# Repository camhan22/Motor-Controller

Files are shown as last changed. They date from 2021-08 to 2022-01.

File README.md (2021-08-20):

# Motor-Controller

12-48VDC 65A continuous (150A Peak) 0-100% duty cycle brushed DC motor driver 

Communicates to a master controller through I2C with commands that look like the following:

DSSSSSSS

Where D is the direction (0 or 1) (1 will apply +VDC to Motor+ Terminal) (0 Will apply +VDC to the Motor- Terminal)
S is the duty cycle from 0-100% (This is checked by the software to ensure it is within bounds) (Anything out of bounds is clamped to 100%)

I2C address can be changed with the dip switches on the board and allows up to 8 motor drivers to run at the same time.

Returns a status byte to describe what the controller is doing. If faults are present, there are seperate status codes for each failure and can be found within the code folder in the controller status codes excel sheet.

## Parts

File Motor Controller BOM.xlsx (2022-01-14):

Schematic Annotation | Part Number | Description | Qty | Price | Supplier | Total Cost | Link
C7,C10,C11,C12 | 399-17501-1-ND | ±5% 50V Ceramic Capacitor X7R 1812 (4532 Metric) 0.1uF | 4 | $1.09 | Digikey | $4.36 | https://www.digikey.com/en/products/detail/kemet/C1812C104J5RAC7800/2235598
C8 | 445-173162-1-ND | 1 µF ±10% 100V Ceramic Capacitor X7R Radial | 1 | $0.73 | Digikey | $0.73 | https://www.digikey.com/en/products/detail/tdk-corporation/FG16X7R2A105KNT06/5811767
C3,C4 | 1189-4388-ND | 2200 µF 50 V Aluminum Electrolytic Capacitors Radial, Can - 10000 Hrs @ 105°C | 2 | $2.84 | Digikey | $5.68 | https://www.digikey.com/en/products/detail/rubycon/50ZLJ2200M18X25/10437363
C9 | 478-10901-1-ND | CAP CER 620PF 100V NP0 1210 | 1 | $0.49 | Digikey | $0.49 | https://www.digikey.com/en/products/detail/avx-corporation/12101A621JAT2A/1605218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
R3,R4,R9,R10 | 541-15.0KACCT-ND | 15 kOhms ±1% 0.75W, 3/4W Chip Resistor 2010 (5025 Metric) Automotive AEC-Q200 Thick Film | 4 | $0.30 | Digikey | $1.20 | https://www.digikey.com/en/products/detail/vishay-dale/CRCW201015K0FKEF/1198590
D1 | 1080-1419-1-ND | Green 570nm LED Indication - Discrete 2.1V 1206 (3216 Metric) | 1 | $0.37 | Digikey | $0.37 | https://www.digikey.com/en/products/detail/QTLP650D4TR/1080-1419-1-ND/2676153?itemSeq=373167869
D2 | 1516-QBLP601-RYCT-ND | Red, Yellow 630nm Red, 591nm Yellow LED Indication - Discrete 2V Red, 2V Yellow 0603 (1608 Metric) | 1 | $0.43 | Digikey | $0.43 | https://www.digikey.com/en/products/detail/qt-brightek-qtb/QBLP601-RY/10322678
R7,R8 | 311-150LJCT-ND | 150 Ohms ±1% 0.25W, 1/4W Chip Resistor 1206 (3216 Metric) Automotive AEC-Q200, Moisture Resistant Thick Film | 2 | $0.10 | Digikey | $0.20 | https://www.digikey.com/en/products/detail/AC1206FR-07150RL/311-150LJCT-ND/2828161?itemSeq=373168587
Q1-Q4 | IRFS3306TRLPBFCT-ND | N-Channel 60 V 120A (Tc) 230W (Tc) Surface Mount D2PAK | 4 | $2.58 | Digikey | $10.32 | https://www.digikey.com/en/products/detail/infineon-technologies/IRFS3306TRLPBF/1925291
U3 | 620-1772-1-ND | Motor Driver NMOS Parallel | 1 | $1.64 | Digikey | $1.64 | https://www.digikey.com/en/products/detail/allegro-microsystems/A4956GESTR-T/5809983
U1 | 175-MAX17640BATA+-ND | Buck Switching Regulator IC Positive Fixed 5V 1 Output 400mA 8-WFDFN | 1 | $1.65 | Digikey | $1.65 | https://www.digikey.com/en/products/detail/maxim-integrated/MAX17640BATA/14287859
L1 | 587-3070-1-ND | 68 µH Unshielded Wirewound Inductor 410 mA 1.3Ohm Max 1210 (3225 Metric) | 1 | $0.30 | Digikey | $0.30 | https://www.digikey.com/en/products/detail/CBC3225T680KR/587-3070-1-ND/2763495?itemSeq=371798502
C6 | 1276-CL32B226MOJVPNECT-ND | 22 µF ±20% 16V Ceramic Capacitor X7R 1210 (3225 Metric) | 1 | $0.71 | Digikey | $0.71 | CL32B226MOJVPNE Samsung Electro-Mechanics | Capacitors | DigiKey (https://www.digikey.com/en/products/detail/samsung-electro-mechanics/CL32B226MOJVPNE/11487778)
C1,C2,C5 | 2873-C1210X105K101TCT-ND | 1 µF ±10% 100V Ceramic Capacitor X7R 1210 (3225 Metric) | 3 | $0.35 | Digikey | $1.05 | https://www.digikey.com/en/products/detail/holy-stone-enterprise-co-ltd/C1210X105K101T/13279995
J1,J2,J4,J5 | 732-10888-1-ND | Pin Screw Terminal, Power Tap M5 Through Hole | 4 | $4.59 | Digikey | $18.36 | https://www.digikey.com/en/products/detail/w%C3%BCrth-elektronik/74650195R/6643984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
J3 | 23-0022292051-ND | Connector Header Through Hole 5 position 0.100" (2.54mm) | 1 | $1.43 | Digikey | $1.43 | https://www.digikey.com/en/products/detail/molex/0022292051/1130591
J3 Conn | 23-0010112053-ND | 5 Rectangular Connectors - Housings Receptacle White 0.100" (2.54mm) | 1 | $0.29 | Digikey | $0.29 | https://www.digikey.com/en/products/detail/molex/0010112053/171981
J3 Crimp | WM23941CT-ND | Non-Gendered Contact Gold 24-30 AWG Crimp - | 9 | $0.39 | Digikey | $3.51 | https://www.digikey.com/en/products/detail/molex/0008550124/1784904
SW1 | 2223-DS04-254-2-03BK-SMT-ND | Dip Switch SPST Position Surface Mount Slide (Standard) Actuator 25mA 24VDC | 1 | $0.54 | Digikey | $0.54 | https://www.digikey.com/en/products/detail/cui-devices/DS04-254-2-03BK-SMT/11310920
JP1,JP2 | 764-THJP2512AST1CT-ND | Thermal Interface Products Therm Jumper 30 mil 2512 | 2 | $1.35 | Digikey | $2.70 | https://www.digikey.com/en/products/detail/vishay-dale-thin-film/THJP2512AST1/11313289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
 | 277-11158-ND | Ring Terminal Connector M5 Stud Circular 10-14 AWG Crimp | 4 | $0.26 | Digikey | $1.04 | https://www.digikey.com/en/products/detail/phoenix-contact/3240084/3603842
R1,R2,R5,R6 | RMCP2010JT100RCT-ND | 100 Ohms ±5% 1W Chip Resistor 2010 (5025 Metric) Automotive AEC-Q200 Thick Film | 4 | $0.41 | Digikey | $1.64 | https://www.digikey.com/en/products/detail/stackpole-electronics-inc/RMCP2010JT100R/2502808
U2 | ATTINY4313-MMHRCT-ND | 8-bit Microcontrollers - MCU AVR 4KB FL 256B SRAM 256B 20MHz 1.8-5.5V | 1 | $0.97 | Digikey | $0.97 | https://www.digikey.com/en/products/detail/microchip-technology/ATTINY4313-MMHR/3046321
 |  |  |  |  | Total Cost | $59.61

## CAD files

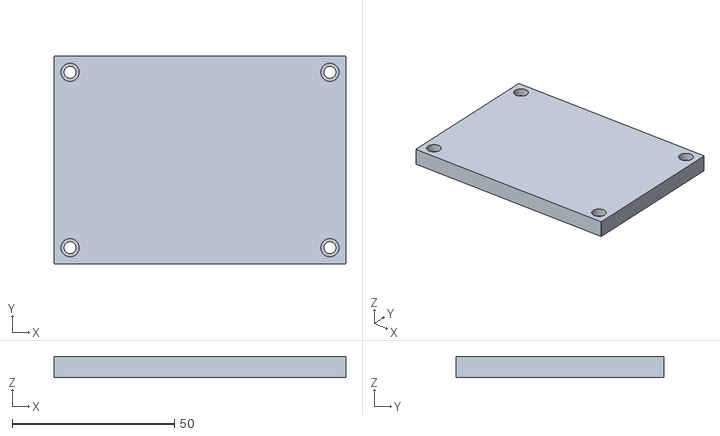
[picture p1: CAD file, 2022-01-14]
Case Top.stl
89.9 x 63.9 x 6.50

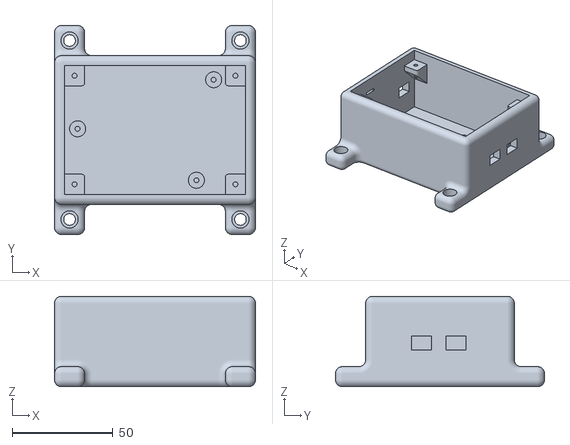
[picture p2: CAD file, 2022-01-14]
Case Bottom.stl
100.0 x 104.0 x 45.0

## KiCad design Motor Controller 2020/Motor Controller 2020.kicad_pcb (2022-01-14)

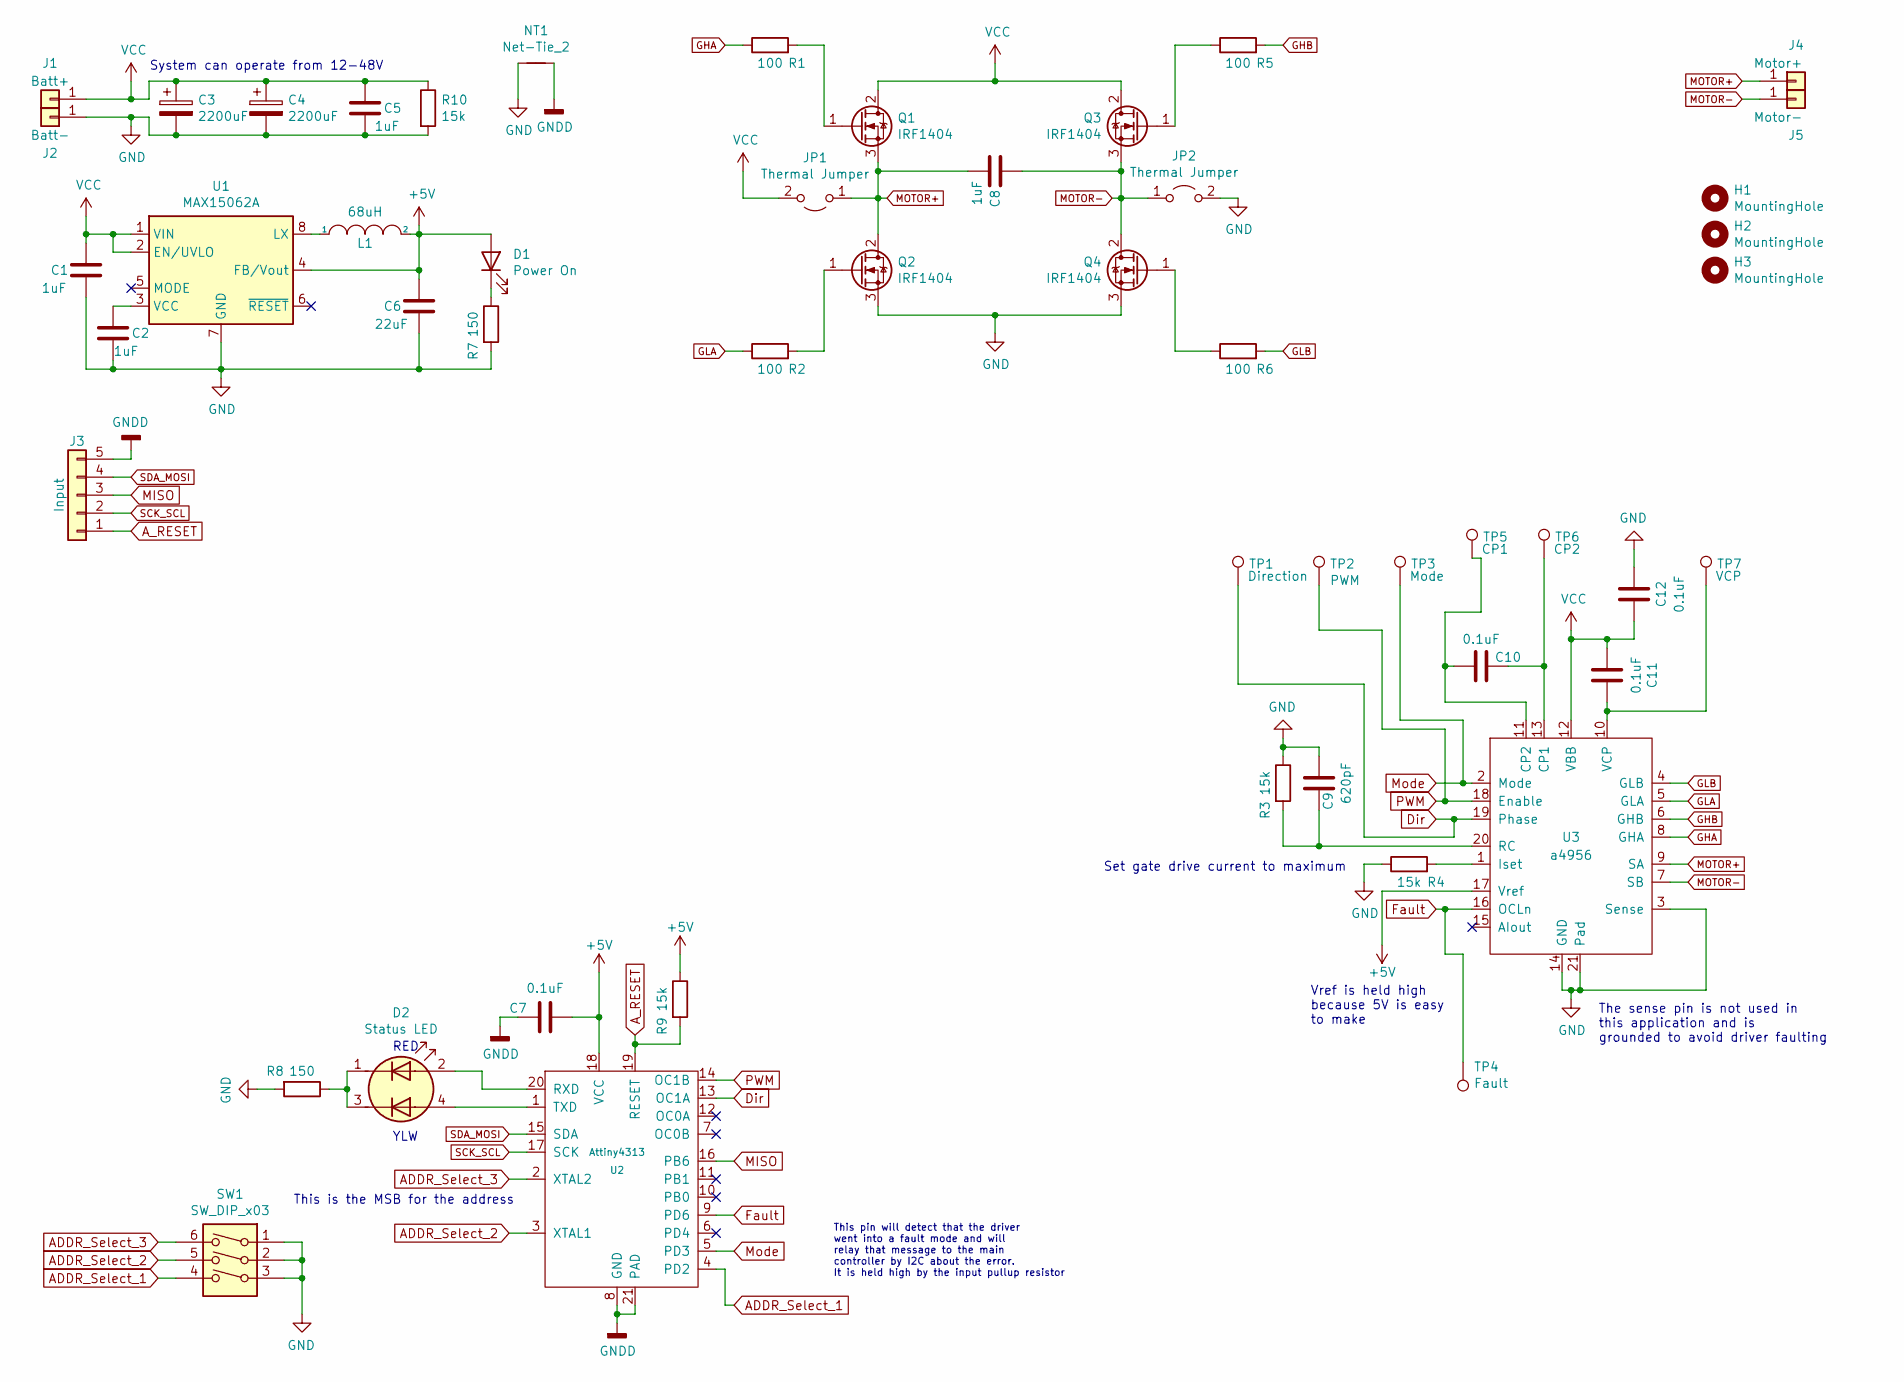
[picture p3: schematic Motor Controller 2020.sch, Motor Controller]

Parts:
C1, C2, C5: 1uF; C_1210_3225Metric
C3, C4: 2200uF; C_Radial_D18.0mm_H35.5mm_P7.50mm
C6: 22uF; C_1210_3225Metric
C7, C10, C11, C12: 0.1uF; C_1812_4532Metric_Pad1.57x3.40mm_HandSolder
C8: 1uF; C_Disc_D5.0mm_W2.5mm_P2.50mm
C9: 620pF; C_1210_3225Metric
D1: Power On; LED_1206_3216Metric
D2: Status LED; LED_0603_4_pin
H1, H2, H3: MountingHole; MountingHole_3.2mm_M3
J1: Batt+; Wuerth_REDCUBE-THR_WP-THRBU_74650195_THR
J2: Batt-; Wuerth_REDCUBE-THR_WP-THRBU_74650195_THR
J3: Input; Molex_KK-254_AE-6410-05A_1x05_P2.54mm_Vertical
J4: Motor+; Wuerth_REDCUBE-THR_WP-THRBU_74650195_THR
J5: Motor-; Wuerth_REDCUBE-THR_WP-THRBU_74650195_THR
JP1, JP2: Thermal Jumper; R_2512_6332Metric
L1: 68uH; L_1210_3225Metric
NT1: Net-Tie_2; NetTie-2_SMD_Pad2.0mm
Q1, Q2, Q3, Q4: IRF1404; TO-263-2
R1, R2, R5, R6: 100; R_2010_5025Metric
R3, R4: 15k; R_2010_5025Metric_Pad1.40x2.65mm_HandSolder
R7, R8: 150; R_1206_3216Metric
R9, R10: 15k; R_1206_3216Metric
SW1: SW_DIP_x03; SW_DIP_SPSTx03_Slide_6.7x9.18mm_W8.61mm_P2.54mm_LowProfile
TP1: Direction; TestPoint_Pad_D1.0mm
TP2: PWM; TestPoint_Pad_D1.0mm
TP3: Mode; TestPoint_Pad_D1.0mm
TP4: Fault; TestPoint_Pad_D1.0mm
TP5: CP1; TestPoint_Pad_D1.0mm
TP6: CP2; TestPoint_Pad_D1.0mm
TP7: VCP; TestPoint_Pad_D1.0mm
U1: MAX15062A; DFN-8_2x2mm_P0.5mm
U2: Attiny4313; VQFN-20-1EP_3x3mm_P0.4mm_EP1.7x1.7mm_ThermalVias
U3: a4956; MLF-20-1EP_4x4mm_P0.5mm_EP2.6x2.6mm_ThermalVias

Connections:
+5V: C6.1, C7.2, D1.2 (A), L1.2, R9.1, U1.4 (FB/Vout), U2.18 (VCC), U3.17 (Vref)
ADDR_Select_1: SW1.4, U2.4 (PD2)
ADDR_Select_2: SW1.5, U2.3 (XTAL1)
ADDR_Select_3: SW1.6, U2.2 (XTAL2)
A_RESET: J3.1, R9.2, U2.19 (RESET)
Dir: TP1.1, U2.13 (OC1A), U3.19 (Phase)
Fault: TP4.1, U2.9 (PD6), U3.16 (OCLn)
GHA: R1.1, U3.8 (GHA)
GHB: R5.2, U3.6 (GHB)
GLA: R2.1, U3.5 (GLA)
GLB: R6.2, U3.4 (GLB)
GND: C1.2, C2.2, C3.2, C4.2, C5.2, C6.2, C9.2, C12.1, J2.1, JP2.2 (B), NT1.1, Q2.3 (S), Q4.3 (S), R3.1, R4.1, R7.2, R8.2, R10.2, SW1.1, SW1.2, SW1.3, U1.7 (GND), U3.3 (Sense), U3.14 (GND), U3.21 (Pad)
GNDD: C7.1, J3.5, NT1.2, U2.8 (GND), U2.21 (PAD)
MISO: J3.3, U2.16 (PB6)
MOTOR+: C8.2, J4.1, JP1.1 (A), Q1.3 (S), Q2.2 (D), U3.9 (SA)
MOTOR-: C8.1, J5.1, JP2.1 (A), Q3.3 (S), Q4.2 (D), U3.7 (SB)
Mode: TP3.1, U2.5 (PD3), U3.2 (Mode)
unnamed: C2.1, U1.3 (VCC)
unnamed: C9.1, R3.2, U3.20 (RC)
unnamed: C10.1, TP6.1, U3.13 (CP1)
unnamed: C10.2, TP5.1, U3.11 (CP2)
unnamed: C11.2, TP7.1, U3.10 (VCP)
unnamed: D1.1 (K), R7.1
unnamed: D2.1 (A1), D2.3 (A2), R8.1
unnamed: D2.2 (K1), U2.20 (RXD)
unnamed: D2.4 (K2), U2.1 (TXD)
unnamed: L1.1, U1.8 (LX)
unnamed: Q1.1 (G), R1.2
unnamed: Q2.1 (G), R2.2
unnamed: Q3.1 (G), R5.1
unnamed: Q4.1 (G), R6.1
unnamed: R4.2, U3.1 (Iset)
PWM: TP2.1, U2.14 (OC1B), U3.18 (Enable)
SCK_SCL: J3.2, U2.17 (SCK)
SDA_MOSI: J3.4, U2.15 (SDA)
VCC: C1.1, C3.1, C4.1, C5.1, C11.1, C12.2, J1.1, JP1.2 (B), Q1.2 (D), Q3.2 (D), R10.1, U1.1 (VIN), U1.2 (EN/UVLO), U3.12 (VBB)

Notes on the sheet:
This pin will detect that the driver went into a fault mode and will relay that message to the main controller by I2C about the error. It is held high by the input pullup resistor
This is the MSB for the address
The sense pin is not used in this application and is grounded to avoid driver faulting
Vref is held high because 5V is easy to make
Set gate drive current to maximum
System can operate from 12-48V
YLW
RED

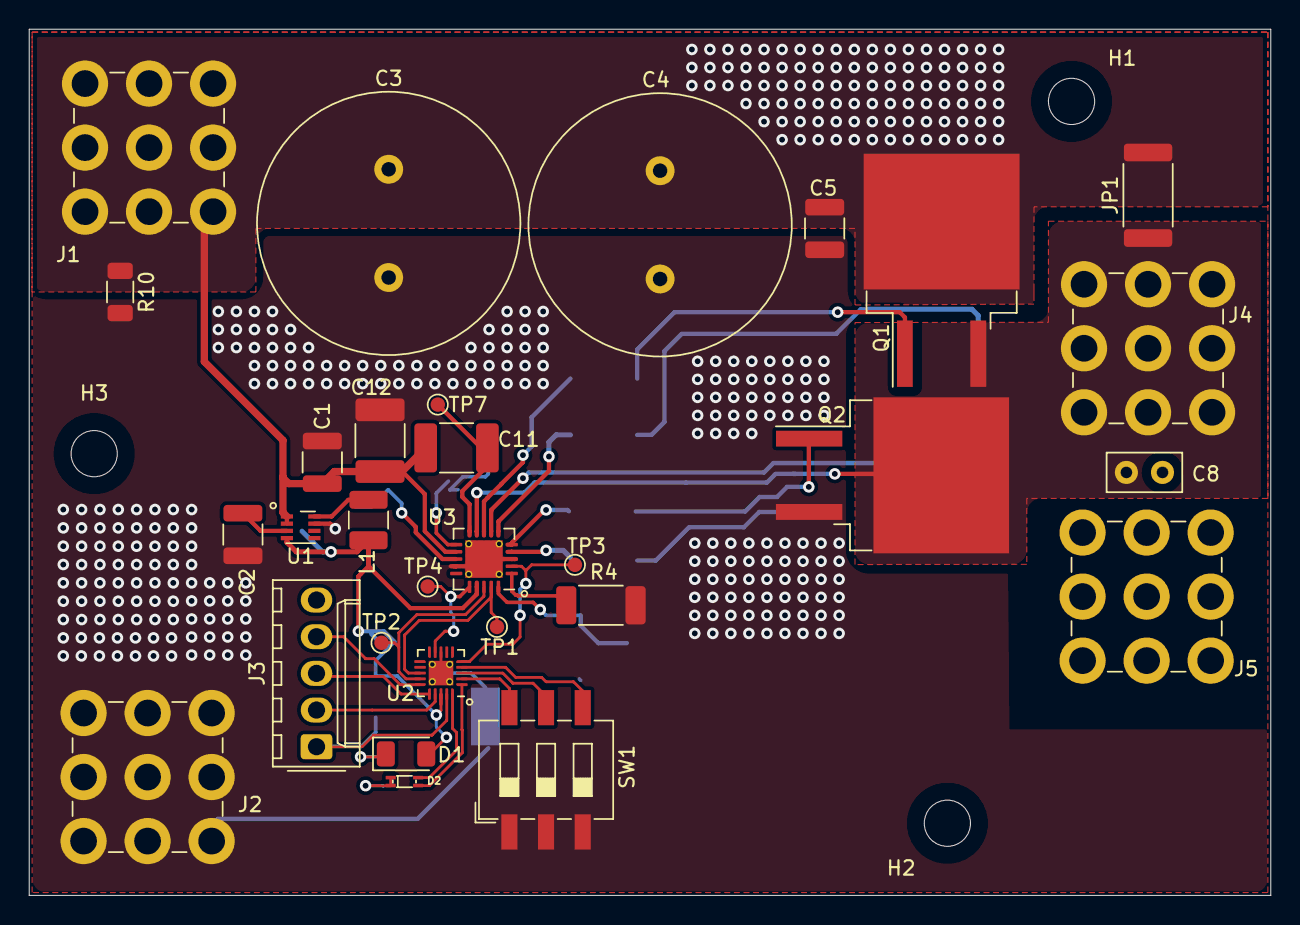
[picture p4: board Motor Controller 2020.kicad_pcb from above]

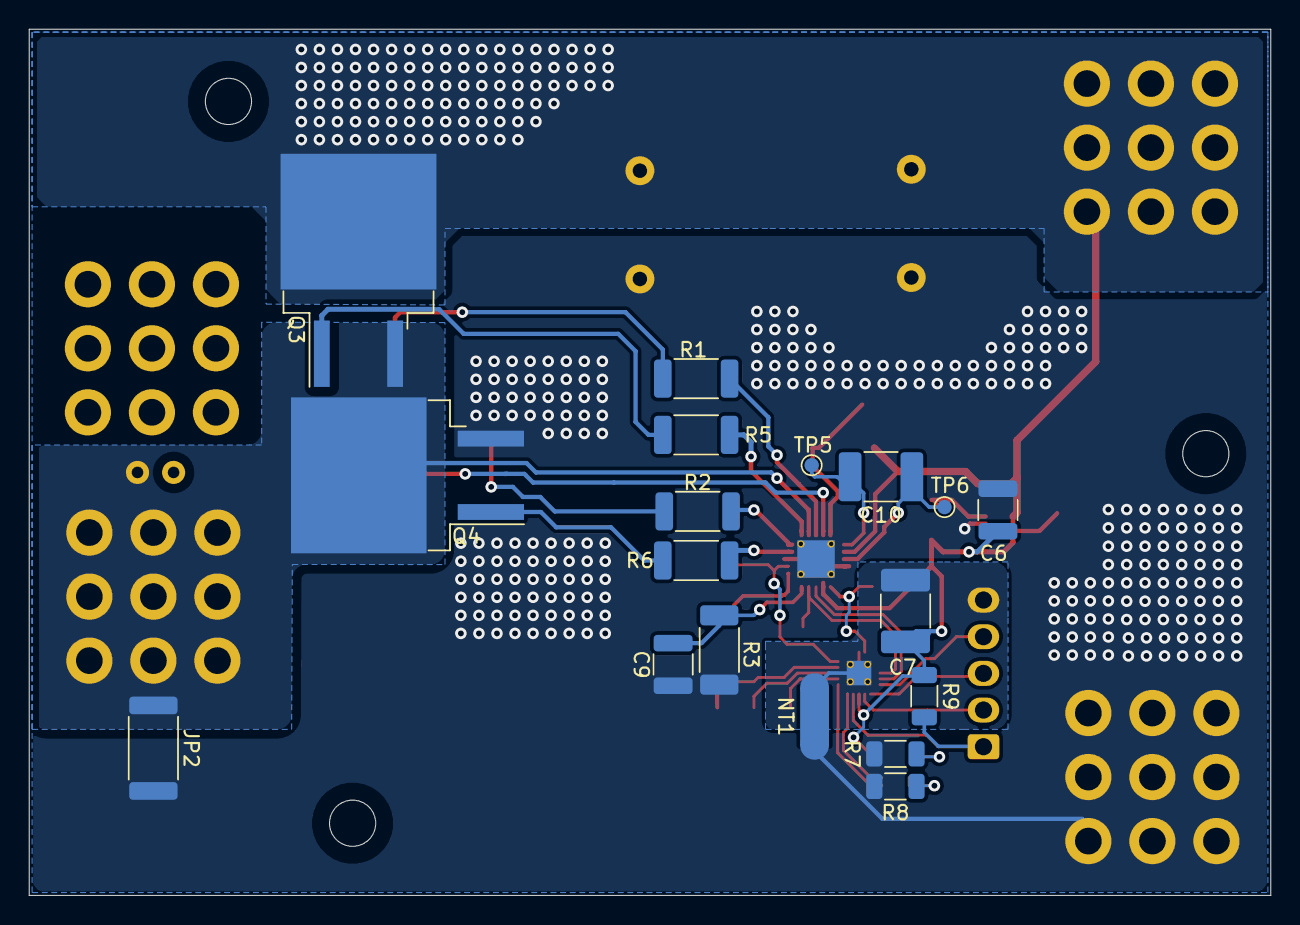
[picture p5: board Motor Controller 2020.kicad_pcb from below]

Board: 2 copper layers, 86.0 x 60.0 mm, 51 parts (18 on the bottom side), 36 nets.

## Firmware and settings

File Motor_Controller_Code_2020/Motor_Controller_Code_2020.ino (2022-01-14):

/*
   MOTOR CONTROLLER CODE 2020
   BY: CAMERON HANSON
   REVISION: 3.1
   RELEASE DATE: 10/18/2021

   RELEASE NOTES:
   V3.1: Changed how address selection is done to have consistency with the PCB
   V3.0: Added CRC check for incoming data to ensure that the data was actually valid, this avoids a problem where spotty connections can lead to the system randomly jumping and going out of control
   V2.3: Added status LED indication to help diagnose problems without a computer being attached. Also added a DEADBAND to the throttle to avoid wasting power
   V2.2.2: Added code to check that duty cycle was within bounds of 0-100%. If it is beyond the bounds, it gets set to the appropriate bound
   V2.2.1: Fixed a bug with the reset driver where PB4 was not being set as an output and the reset process was allowed to be interrupted
   V2.2: Fixed a bug that would have caused the kart to slam to a stop if a false reset code was sent when no controllerFault existed and restructured the code to be more readable
   V2.1: Added controllerFault line from driver chip to code and added some controllerFault codes to be put to the main controller if the driver chip is controllerFaulted
   V2.0: Changed controller to a more robust driver that handles more features of the H-Bridge. The microcontroller just converts the I2C into a PWM and controllerDirectionection for the driver as well as checking controllerFaults)

   THINGS TO UPDATE:

   Definitions:
   Controller - Arduino chip (ATTINY4313)
   Driver - MOSFET driver chip (A4956 motor driver)
   Main Controller - Sends the I2C commands to the motor controller (Acts as the master for all motor controllers) (In my application, it will be a raspberry Pi 4)
*/

//LIBRARIES//
#include <Wire.h> //Add the wire library for the I2C protocol
#include "CRC8.h" //Add the CRC8 library for calculating 8 bit crc values
#include "CRC.h" //Include the CRC library which is used in the crc8 library
//END LIBRARIES//

//DEFINES// These will save a slight amount of space for things that cannot change mid run
#define FREQUENCY 25000 // FREQUENCY of the motor driver (minimum is 1.5kHz due to standby mode timer on the A4956 driver chip)
#define DEADBAND 10 //If the incoming duty cycle is less than this limit, then it will make the motor output a zero PWM signal to avoid wasting power when it cannot move
#define START_UP_DELAY 2000 // Specifies how long to take ramping the controller down
#define RAMP_DOWN_TIME 2000 // Controller must be at zero on I2C for greater than this value to allow user control
#define WATCHDOG_TIME_LIMIT 2000 //Specifies how often the system should get a message in milliseconds
#define DIR_PIN 12 // Tells which pin the controllerDirectionection pin is on
#define MODE_PIN 8 // Defines which pin the mode selector for the driver chip is
#define FAULT_PIN 5 // Defines which pin the fault pin from the driver chip is on
#define STATUS_RED_PIN 0 //Defines which pin the red LED status light is on
#define STATUS_YELLOW_PIN 1 //Defines which pin the yellow LED status light is on
#define STATUS_BLINK_RATE 500 //defines how long each state will last. Total blink time is twice this.
//The above 2 pins need to be flipped in order to make this work with the new board design

//USER FUNCTIONS//
void setup_Fast_PWM(); // Sets up the PWM pins
void recieve_Event(int howMany); // Function that gets called when data is delivered to the motor driver
void request_Event(); // Function to send data back to the master controller

void set_Speed_and_Direction();// Function to set the speed and direction of the controller
void kill_Motors(bool emergency); // Function to shut down the motors (If the boolean inside is set, then it will instantly kill the motors
void reset_Driver(); //Function to reset driver chip
bool is_Data_Good(byte data, byte crc); //Function to check I2C CRC data to make sure data is valid

void wait_Zero_Throttle(); // Function to listen to I2C communication and wait for throttle to be set at zero before it will allow for user control
void check_Reset(byte data); // Checks to see if the system has been issued the reset command
void set_LED_Status(); //Sets the LED lights depending on the status of the system
//END USER FUNCTIONS


//USER PARAMETERS//
//controller physical attributes
byte controllerAddress = 0; // Holds the address of the device. This will be read by dip switches and set inside the setup function

//controller output variables
bool controllerDirection = 1; //Holds the direction the controller should go
int controllerDutyCycle = 0; // Holds the percentage that will be passed to the motor

//controller reset variables
byte resetCount = 0; // Holds a number used to determine if the first byte of a reset command happened
bool resetController = 0; // Holds whether a reset should be initaited
byte dataCount = 0; //Holds how many data bytes have been recieved, a complete packet is 2 bytes (one data and one crc)
byte lastData = 0; //Holds the last recieved data byte for crc checking

//controller status variables
byte controllerStatus = 0; // Tells the controller if there are any problems and if so, what they are (This is requested by the master each loop)
bool controllerFault = 0; // Tells controller if it is controllerFaulted or not. This can be cleared by sending a specific command to the controller

//last update times
unsigned long lastReceiveTime = 0; // Holds when the last time an I2C command was given to the board
unsigned long lastStatusTime = 0; //Holds the last time the LED changed state

//crc variable
CRC8 incoming_CRC; //Create a CRC object to test whether data is good
//END USER PARAMETERS//

void setup() {
  //Set the controllerAddress lines to be inputs with pull-ups
  pinMode(2, INPUT_PULLUP); // MSB
  pinMode(3, INPUT_PULLUP);
  pinMode(4, INPUT_PULLUP); // LSB

  //Read the controllerAddress values on startup and connect to the I2C bus as that controllerAddress
  bool controllerAddress_b2 = !digitalRead(2); // MSB
  bool controllerAddress_b1 = !digitalRead(3);
  bool controllerAddress_b0 = !digitalRead(4); // LSB

  //Order the bits to give the correct controllerAddress for the I2C bus
  controllerAddress |= controllerAddress_b2 << 2; // Shift the MSB by two positions
  controllerAddress |= controllerAddress_b1 << 1; // Shift the middle bit by 1
  controllerAddress |= controllerAddress_b0; //  Add the last bit to the controllerAddress

  incoming_CRC.setPolynome(0xD5); //Polynomial to use for CRC generation (Uses standard CRC-8 polynome)

  //Put the controller in slow decay mode (Braking)
  pinMode(MODE_PIN, OUTPUT);
  digitalWrite(MODE_PIN, HIGH);

  // Define the controllerFault pin from the driver as an input with pullup
  pinMode(FAULT_PIN, INPUT_PULLUP);

  //Set the controllerDirection pin as an output
  pinMode(DIR_PIN, OUTPUT);

  //Set status lights as outputs
  pinMode(STATUS_RED_PIN, OUTPUT);
  pinMode(STATUS_YELLOW_PIN, OUTPUT);

  //Set the status lights to off in the beginning
  digitalWrite(STATUS_RED_PIN, LOW);
  digitalWrite(STATUS_YELLOW_PIN, LOW);

  setup_Fast_PWM(); // Setup and start hardware PWM generator (MUST DO THIS FIRST!!!!) (Messes up some bits in the port that controls the I2C bus)
  reset_Driver(); //Reset the driver chip on controller startup

  Wire.begin(controllerAddress);// join i2c bus with controllerAddress that was read by the dip switches (This needs to be unique for each controller on the system)
  Wire.onReceive(recieve_Event); // Add an event to the arduino for receiving I2C communications
  Wire.onRequest(request_Event); // Add an event for when the controller is requested to give information


  wait_Zero_Throttle(); // Wait until the throttle has been reset to 0% PWM to ensure it doesn't takeoff unexpectedly
}

void loop() {
  if (controllerFault == 1) { //If there is an active fault, wait for a reset event, it is the only thing the controller should be doing
    if (resetController == 1) { //Wait for a reset event to come in
      reset_Driver(); // Reset the driver chip just to make sure any faults are cleared since they can cause the system to fail
      wait_Zero_Throttle();  // If the system was reset, wait for the throttle to go to zero before giving control back
      controllerFault = 0; // Make sure the fault flag is cleared since the system is no longer faulted
      resetController = 0; // The reset has been completed
      controllerStatus = 0; // The system should be good after this
    }
  } else { //If no active controllerFaults exist, check for new ones and if none exist, then set the speed and direction
    if (millis() - lastReceiveTime > WATCHDOG_TIME_LIMIT) { // Check if commands have stopped for too long
      controllerStatus = 1;
      controllerFault = 1;
      kill_Motors(0); //Kill the motors but shutdown in non-emergency way
    }

    // If the driver chip is in fault mode, then let the arduino know. There isn't a way  to tell why the driver has failed but there are only a few causes
    // Causes: A VDS fault has occured meaning it saw too much voltage across the mosfet and could be damaged
    // Causes: Internal current limit has tripped (This is disabled in this version and cannot occur)
    if (digitalRead(FAULT_PIN) == 0) {
      controllerFault = 1;
      controllerStatus = 2; // This code means the driver chip has faulted in some way. Can be reset by sending a reset command to the controller
      kill_Motors(0); //Kill the motors but shutdown in non-emergency way
    }
    set_LED_Status(); //Set the status LEDs
    set_Speed_and_Direction(); // Set the speed and direction of the motor driver (If any controllerFaults occur on the way, the duty cycle will be set to zero by the time it gets here)
    delay(10); //Delay the system from updating too often (having higher refresh rate may help with VDS controllerFaults since the changes will be smaller
  }
}

void setup_Fast_PWM() {
  //Function to setup the Hardware PWM generators. Clears the pins at compare match and sets them at top
  //FAST PWM mode with ICR1 as the top value for the PWM (Mode 14)(Sets the PWM FREQUENCY)
  //Sets OC1B to output the PWM signal
  //Uses internal 8MHz clock (Makes the board easier and cheaper to manufacture) (Actual PWM FREQUENCY is not that important due to openloop control)

  TCCR1A |= (1 << COM1B1) + (1 << WGM11); //Set B channel to clear at compare match and set at top
  TCCR1B |= (1 << WGM12) + (1 << WGM13) + (1 << CS10); // No prescaling
  ICR1 = 8000000 / FREQUENCY - 1; //Calculates the FREQUENCY of the PWM pins
  OCR1B = 0; // Set to zero to decontrollerFault the controller at startup
  DDRB |= (1 << PB4); //Pin 14 on the chip should be an output
}

void recieve_Event(int howMany) {
  // function that executes whenever data is received from master
  // this function is registered as an event
  byte recieve_byte = Wire.read();    // receive byte as an integer (MUST DO THIS FIRST!!!!!!! otherwise a NACK will occur due to it taking too long to read)
  byte crc_byte = Wire.read(); //Read in the crc byte from the bus

  if (is_Data_Good(recieve_byte, crc_byte) == 1) { //Check if the last recieved byte (the data) crc and the current byte (the crc) are the same
    lastReceiveTime = millis(); //Update the last time a command was recieved

    controllerDirection = bitRead(recieve_byte, 7); //Mask of the upper bit for the direction and shift it 7 places to be in the LSB which can be stored in a bool
    controllerDutyCycle = recieve_byte & (B01111111); //Mask off the lower 7 bits and convert them to an int. (Need to get rid of the direction bit)

    if (controllerDutyCycle > 100) { //If the duty cycle is greater than 100, just set it to 100
      controllerDutyCycle = 100;
    } else if (controllerDutyCycle < DEADBAND) { //If the duty cycle is less than 0, set it to 0
      controllerDutyCycle = 0;
    }
  }
}

void request_Event() {
  Wire.write(controllerStatus); // Give the main controller the status of this motor driver (0 means everything is okay)(1 means a watchdog timeout)
}

void set_Speed_and_Direction() {
  if (controllerDirection == 1) {
    OCR1B = map(controllerDutyCycle, 0, 100, 0, 8000000 / FREQUENCY - 1); // Map the 0-100% duty cycle to the counts needed to make the PWM that duty cycle
    digitalWrite(DIR_PIN, HIGH); // Set the direction pin to be high
  }
  if (controllerDirection == 0) {
    OCR1B = map(controllerDutyCycle, 0, 100, 0, 8000000 / FREQUENCY - 1);
    digitalWrite(DIR_PIN, LOW); // Set the direction pin to be low
  }
}

void kill_Motors(bool emergency) { //Function to kill the motors
  int delay_time;
  controllerDutyCycle = 0; //If the motors need to be shut down, make sure the command driving them is also turned off
  if (emergency) { // If it is an emergency, stop the motors immediately
    OCR1B = 0;
  } else {
    delay_time = RAMP_DOWN_TIME / OCR1B; // Determine how long to take between decrements to meet the stop time
    for (int i = OCR1B; i > 0; i--) { // Decrement from the current value to zero
      OCR1B = i;
      delay(delay_time); // Delay between each decrement to make it smooth, the length of this delay is determined by how long it should take for the system to slow down
    }
  }
}

//The watchdog is not needed here because if the I2C disappears during the startupdelay, the value will still be zero after exiting and then will be detected by the watchdog timer in the normal loop which will then controllerFault out if enough time passes by
void wait_Zero_Throttle() {
  unsigned long start_time = millis();
  int elapsed_time = 0;
  controllerStatus = 15; //This code means the system is waiting for the input to be zero

  while (millis() - start_time < START_UP_DELAY) { //While the START_UP_DELAY timer has not elapsed
    if (controllerDutyCycle >= DEADBAND) { //If the duty cycle ever goes above the deadband zone, reset the timer
      start_time = millis();
    }
  }
  controllerStatus = 0; // Once we make it through this code, reset the status so the main controller knows everything is good
}

void check_Reset(byte data) { // Checks to see if the system has been issued the reset command
  if (data == 112) { // If the byte coming in is 112 (Normally not something sent to the controller) then increase the counter
    resetCount++;
  } else if (resetCount >= 1 && data == 229 && controllerFault == 1) {// If the first byte is 112 and the next byte is 229, then the fault will be allowed to clear
    resetController = 1;
    resetCount = 0;
  } else {  //otherwise reset the counter
    resetCount = 0;
  }
}

void reset_Driver() {
  noInterrupts(); //Disable interrupts because it can screw up the timing if a recieve event comes in while this is happening
  TCCR1A = 0; //Set PORTB to be normal operation (timer stopped)
  TCCR1B = 0;
  DDRB |= (1 << PB4); //Set PB4 to be an output (It already was an output, but this makes sure that setting the TCCR1A and TCCR1B registers to 0 didn't affect it)

  PORTB &= ~(1 << PB4); // Write a 0 to PB4 (Enable pin on driver)
  delay(10); // Allow the system to go into standby mode (only need 1ms but 10x longer ensures it is in standby)
  PORTB |= (1 << PB4); // Write a 1 to PB4
  delayMicroseconds(50); //Wake the system from standby(Datasheet says it only need ~20us, so 50us should be good enough)
  PORTB &= ~(1 << PB4); //Write a zero to stop it from being active during the reset
  delayMicroseconds(400); //Delay 400us to ensure the driver has been started properly before continuing (The actual time of this doesn't matter as long as it is not greater than 700us since that is the shortest time to standy for the driver chip)

  setup_Fast_PWM();
  interrupts(); //Allow interrupts after the driver chip is fully reset
}

bool is_Data_Good(byte data, byte crc) {
  incoming_CRC.restart(); //Reset the crc polynomial to default conditions
  incoming_CRC.add(data); //Add the recieved data byte to the crc check
  return incoming_CRC.getCRC() == crc ? 1 : 0; //If the crc's match, then return that data is good
}

void set_LED_Status() {
  if (controllerStatus == 0) { //If the controller is working properly, then turn the status off
    digitalWrite(STATUS_RED_PIN, LOW);
    digitalWrite(STATUS_YELLOW_PIN, LOW);
  } else if (controllerStatus == 15) { //If the controller is waiting for the throttle to reset, put the yellow light on to indicate that
    digitalWrite(STATUS_RED_PIN, LOW);
    digitalWrite(STATUS_YELLOW_PIN, HIGH);
  } else if (controllerStatus == 1) { //If the driver is controllerFaulted due to a communication issue, set the red led to on
    digitalWrite(STATUS_RED_PIN, HIGH);
    digitalWrite(STATUS_YELLOW_PIN, LOW);
  } else if (controllerStatus == 2) { //If a VDS controllerFault has occured, blink the red led
    digitalWrite(STATUS_YELLOW_PIN, LOW);
    if (millis() - lastStatusTime > STATUS_BLINK_RATE) {
      digitalWrite(STATUS_RED_PIN, !digitalRead(STATUS_RED_PIN)); //Toggle the red LED
      lastStatusTime = millis(); //Update the last time the state was changed
    }
  }
}

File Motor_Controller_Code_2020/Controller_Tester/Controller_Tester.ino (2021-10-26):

#include <Wire.h>
#include "CRC8.h" //Add the CRC8 library for calculating 8 bit crc values
#include "CRC.h" //Include the CRC library which is used in the crc8 library
#include <Adafruit_GFX.h>
#include <Adafruit_SSD1306.h>


//Defines for OLED screen
#define SCREEN_WIDTH 128 // OLED display width, in pixels
#define SCREEN_HEIGHT 64 // OLED display height, in pixels
#define OLED_RESET     4 // Reset pin # (or -1 if sharing Arduino reset pin)
#define SCREEN_ADDRESS 0x3C ///< See datasheet for Address; 0x3D for 128x64, 0x3C for 128x32

void drawBarGraph(int level); //Function prototype to draw a bar graph at the top of the screen

byte value = 0;
bool dir = 0;
int throttle_val = 50;
int throttle_status = 16;
int motor_status = 15;
CRC8 incoming_CRC; //Create a CRC object to test whether data is good

//Adafruit_SSD1306 display(SCREEN_WIDTH, SCREEN_HEIGHT, &Wire, OLED_RESET); //Create the oled screen variable

void setup() {
  Wire.begin(); // join i2c bus (address optional for master)
  Serial.begin(9600);

  incoming_CRC.setPolynome(0xD5); //Polynomial to use for CRC generation (Uses standard CRC-8 polynome)

  pinMode(5, INPUT_PULLUP); // Pin used to reset the controller
  pinMode(6, INPUT_PULLUP); //Used to set the direction

  //delay(1000);

  /*Wire.beginTransmission(7); // transmit to device #8
  Wire.write(112);              // sends one byte
  Wire.endTransmission();    // stop transmitting

  Wire.beginTransmission(7); // transmit to device #8
  Wire.write(229);              // sends one byte
  Wire.endTransmission();    // stop transmitting
*/
  /*if (!display.begin(SSD1306_SWITCHCAPVCC, SCREEN_ADDRESS)) {
    Serial.println(F("SSD1306 allocation failed"));
    for (;;); // Don't proceed, loop forever
    }*/
}




void loop() {

  /*Wire.requestFrom(8, 2); // Request the controller status from the motor controller
    throttle_val = Wire.read();
    throttle_status = Wire.read();
    if (throttle_status == 16) {
    Wire.beginTransmission(7); // transmit to device #8
    Wire.write(112);              // sends one byte
    Wire.endTransmission();    // stop transmitting

    Wire.beginTransmission(7); // transmit to device #8
    Wire.write(229);              // sends one byte
    Wire.endTransmission();    // stop transmitting
    }

  */
  throttle_val = map(analogRead(A0), 0, 1023, 0, 100);
  dir = digitalRead(6);
  value = bitWrite(throttle_val, 7, dir);

  incoming_CRC.restart(); //Reset the crc polynomial to default conditions
  incoming_CRC.add(value); //Add the recieved data byte to the crc check
  Serial.print(incoming_CRC.getCRC());
  Serial.print(",");

  Wire.beginTransmission(7); // transmit to device #8
  Wire.write(value);              // sends one byte
  Wire.write(incoming_CRC.getCRC()); //Write the CRC value as well
  Wire.endTransmission();    // stop transmitting

  Wire.requestFrom(7, 1); // Request the controller status from the motor controller
  Serial.println(Wire.read());

  if (digitalRead(5) == 0) { // If the reset pin is on, then reset
    Serial.println("Reset");

    Wire.beginTransmission(7); // transmit to device #8
    Wire.write(112);              // sends one byte
    Wire.endTransmission();    // stop transmitting

    Wire.beginTransmission(7); // transmit to device #8
    Wire.write(229);              // sends one byte
    Wire.endTransmission();    // stop transmitting

    delay(2000);
  }

  delay(500);
  /*display.clearDisplay();

    display.setTextSize(2);      // Normal 1:1 pixel scale
    display.setTextColor(SSD1306_WHITE); // Draw white text
    value = bitWrite(throttle_val, 7, 0);
    drawBarGraph(throttle_val);
    display.setCursor(0, 16);     // Start at top-left corner

    String dir_s;
    if (dir == 1) {
    dir_s = "Forward";
    } else {
    dir_s = "Reverse";
    }
    display.write(dir_s.c_str(), dir_s.length());
    display.setCursor(0, 32);     // Start at top-left corner
    display.setTextSize(2);      // Normal 2:1 pixel scale
    String m_s = "Motor: " + (String)(motor_status);
    display.write(m_s.c_str(), m_s.length());


    display.setCursor(0, 48);     // Start at top-left corner
    String c_s = "Throt: " + (String)(throttle_status);
    display.write(c_s.c_str(), c_s.length());
    display.display();
    delay(10);*/
}

/*void drawBarGraph(int level) { //level is between 0 and 100%
  display.setCursor(0, 0);     // Start at top-left corner
  for (int i = 0; i < map(level, 0, 100, 0, 128); i++) {
    display.drawFastVLine(i, 0, 15, SSD1306_WHITE);
  }
  }*/

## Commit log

2021-06-15 Added existing files
    [74650195 (rev1).stp, BOM.xlsx, Controller Status Codes.xlsx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]
2021-06-17 Added reset/program jumper to board
    [BOM.xlsx, Motor Controller 2020.kicad_pcb, Motor Controller 2020.sch]
2021-06-17 Added mounting holes instead of trying to slide the board into the housing
    The 3D printed slide mechanism didn't work because the printer couldn't reproduce the sharp corners
    [91290A111_BLACK-OXIDE CLASS 12.9 SOCKET HEAD CAP SCREW.STEP, BOM.xlsx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]
2021-06-20 Bug fixes and code readability changes
    [Motor_Controller_Code_2020.ino]
2021-06-22 Fixed driver reset bugs
    [Motor Controller 2020.kicad_pcb, Motor Controller 2020.sch]
2021-06-22 Tested Reset Code
    [BOM.xlsx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]
2021-06-30 Updated PCB to DC-DC Converter
    Also changed associated BOM lines. Created a notes document to show what it can do.
    [74650195 (rev1).stp, 91290A111_BLACK-OXIDE CLASS 12.9 SOCKET HEAD CAP SCREW.STEP, Buck 5V BOM.xlsx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]
2021-06-30 Added STL files for case
    [Case.stl, Cover.stl]
2021-06-30 Added motor modeling
    [Cim-Motor Model Parameters.txt, EML Wheel Calculations.xlsx, Go-Kart BOM.xlsx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]
2021-07-01 Updated controller PCB
    Added several capacitors to help with switching transients
    [Buck 5V BOM.xlsx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]
2021-07-02 Updated Controller board
    Separated the logic and power GNDs to minimize noise. Added more Vias for current capability. Rerouted MOSFET tracks to be nearly the same length. Filleted the corners on copper pours. Added more test points for diagnosis.
    [Motor Controller 2020-B_Cu.gbr, Motor Controller 2020-B_Mask.gbr, Motor Controller 2020-B_Paste.gbr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]
2021-07-02 Updated schematic and PCB
    Reduced the loop length to just over half the original length. Added more Vias for stitching. Changed MOSFET to handle up to 48V, meaning that the system can work up to 48V while still maintaining th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
    [Buck 5V BOM.xlsx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]
2021-07-06 Re-arranged components
    [Buck 5V BOM.xlsx, Motor Controller 2020.kicad_pcb, Motor Controller 2020.sch]
2021-07-07 Updated PCB
    Added larger caps for local storage. Also removed 4 MOSFETS because I don't believe I will need them. This will be tested when the system works properly
    [Buck 5V BOM.xlsx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]
2021-07-13 Remade and checked gerber files
    [Motor Controller 2020-B_Cu.gbr, Motor Controller 2020-B_Mask.gbr, Motor Controller 2020-B_Paste.gbr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]
2021-07-13 Update Buck 5V BOM.xlsx
    [Buck 5V BOM.xlsx]
2021-07-22 Made gerber files
    [Buck 5V BOM.xlsx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]
2021-08-06 Added status lights
    Added power and status lights to help diagnose issues when the system is running without screen on the master controller
    [Buck 5V BOM.xlsx, Controller Status Codes.xlsx, Motor Controller 2020.kicad_pcb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]
2021-08-14 Updated Code
    [BOM.xlsx]
2021-08-15 Updated CAD Model
    [Motor Controller 2020.kicad_pcb]
2021-08-20 Housekeeping
    Added datasheets and changed readme
    [Motor Controller BOM.xlsx]
2021-09-07 Updated Parts to match what was bought
    [Buck 5V BOM.xlsx]
2021-10-11 created stl files
    [Case.stl, Cover.stl]
2021-10-19 Updated code and BOM
    Added code to check for a CRC to ensure data is correct.
    Also changed the BOM to allow for a shorter controller design
    [Buck 5V BOM.xlsx, Motor Controller 2020.kicad_pcb, Motor Controller BOM.xlsx]
2021-10-26 Created new version
    Updated PCB and added CRC check for incoming data
    [Motor Controller 2020-B_Cu.gbr, Motor Controller 2020-B_Mask.gbr, Motor Controller 2020-B_Paste.gbr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]
2022-01-14 Updated PCB
    [Case Bottom.stl, Case Top.stl, Case.stl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]
